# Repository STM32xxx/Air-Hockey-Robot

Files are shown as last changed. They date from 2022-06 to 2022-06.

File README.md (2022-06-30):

# Air-Hockey-Robot
使用OpenCV3 + Arduino mega2560，可与人对战的桌上冰球机器人

展示视频：https://www.bilibili.com/video/BV1ax411d7me?share_source=copy_web

-------------------------------------------------------------------------------------------------------------------------

参考项目：https://github.com/JJulio/AHRobot.git

原项目是国外一个大神做的，相关教程也很详细，链接里文档、视频、源码都有，他的球桌甚至都是自己做的，我也试着用三合板做了个球桌，做的有些大了，而且xy平台用的是H-bot结构，这种结构xy轴是联动的，x轴越长，在快速运动时会产生一个使轴旋转的力，导致高速运动时会卡住。

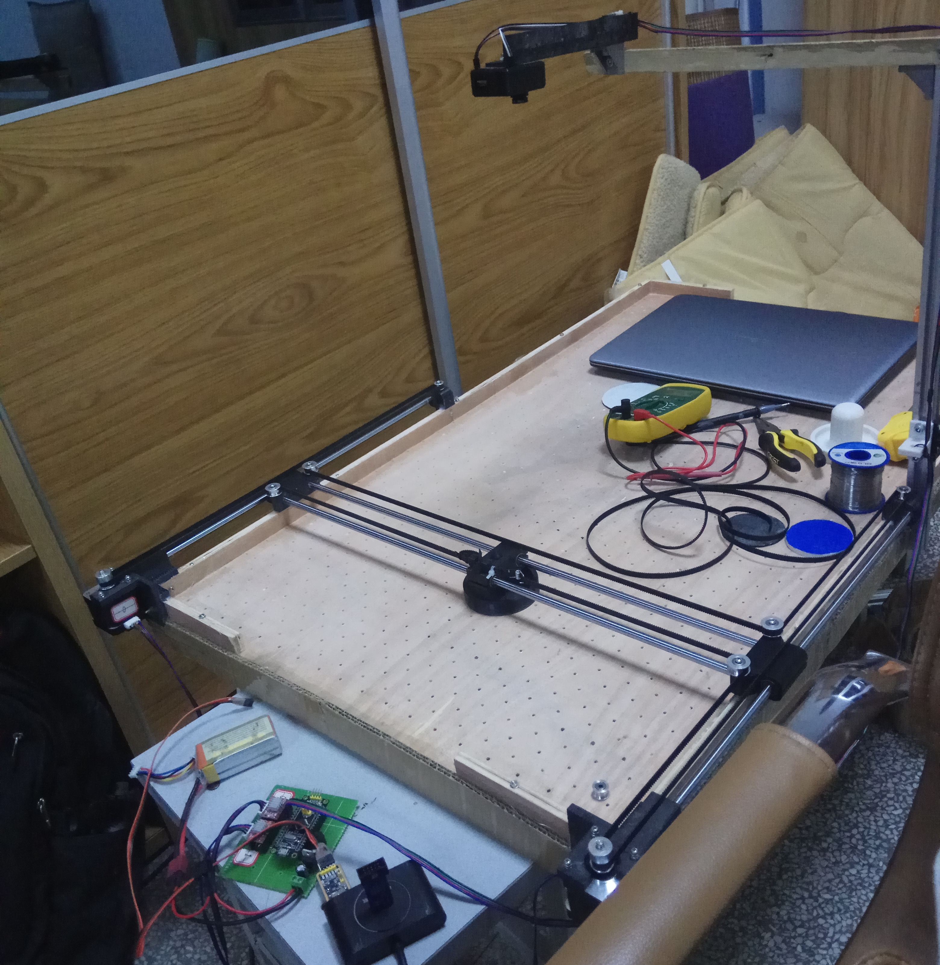
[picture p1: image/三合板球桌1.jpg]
<div align=left>

接下来干脆直接tb买个球桌，长这个样子，81*42cm，比较小，接下来就是将所有机械部分组装上去。

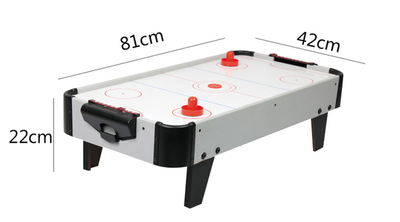
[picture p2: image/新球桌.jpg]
<div align=left>

一些连接件也要自己设计了，用SolidWorks2016设计出以下三维图，黑色的为3D打印件。xy轴是分开控制的，x轴单独由一个电机控制，y轴左右两边各一个电机，这两个电机运动完全同步。

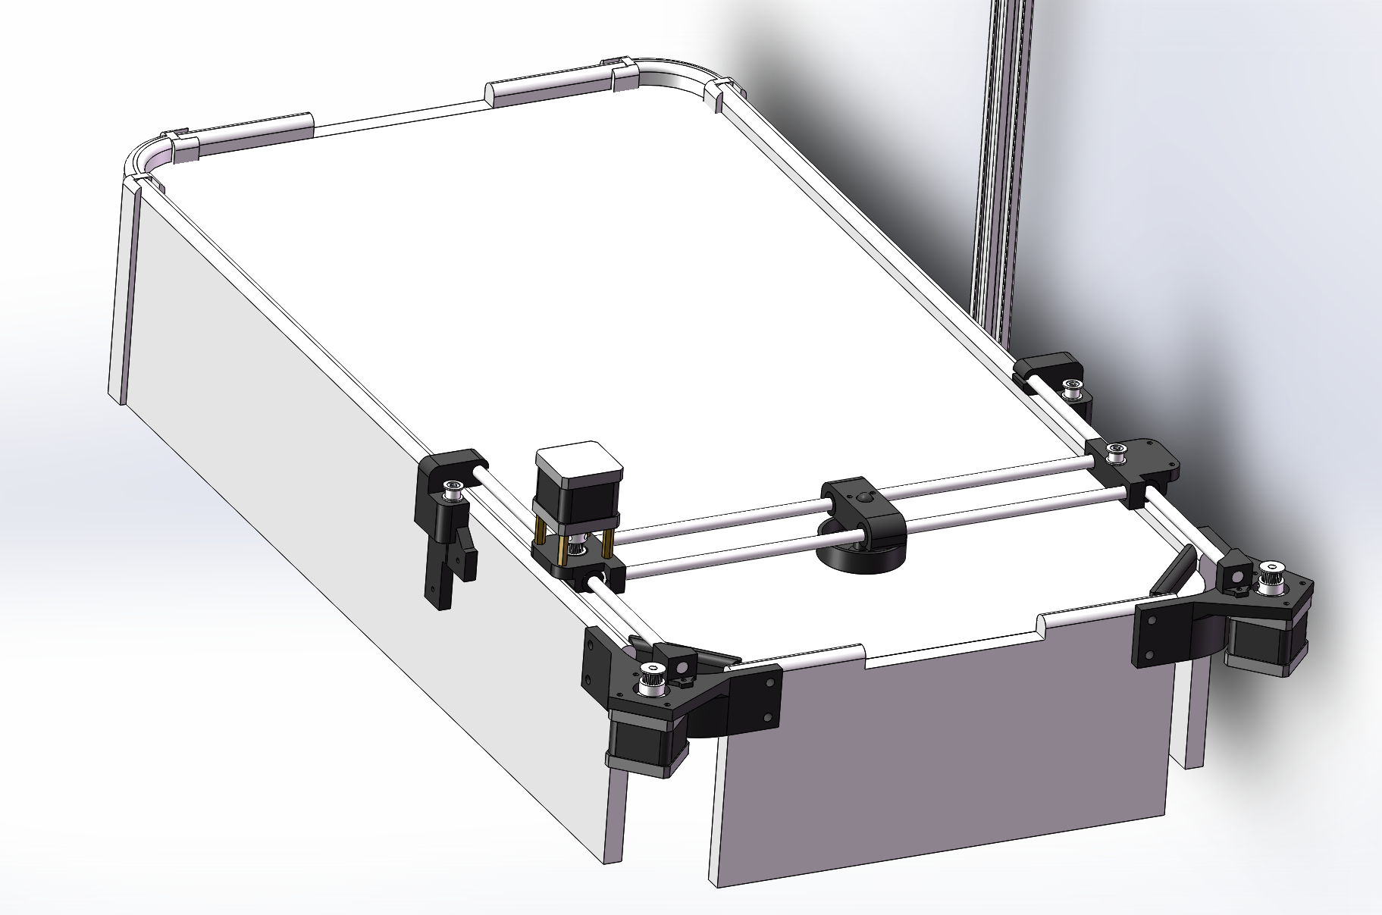
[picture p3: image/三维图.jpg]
<div align=left>

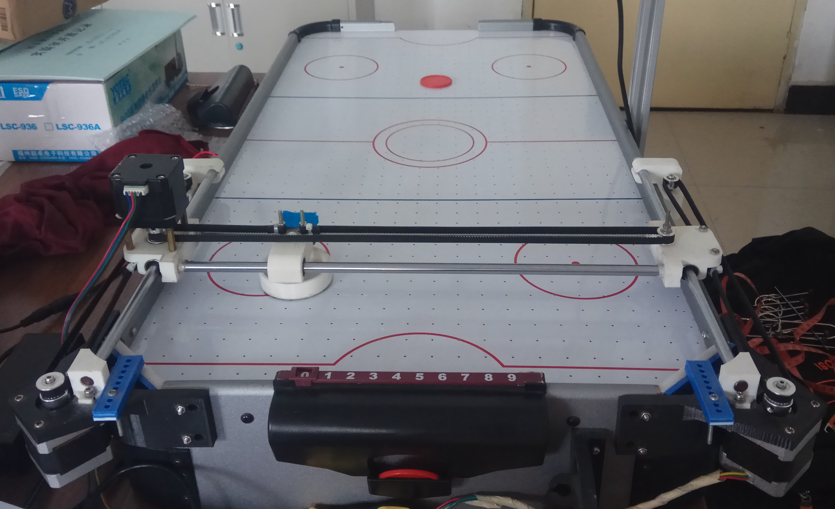
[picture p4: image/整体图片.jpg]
<div align=left>

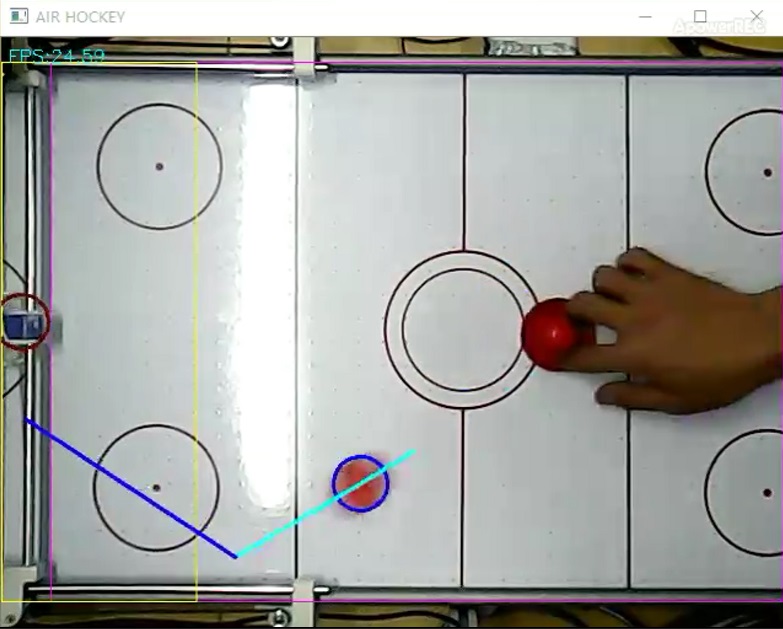
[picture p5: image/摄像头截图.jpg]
<div align=left>

下位机控制采用的arduino mega2560+ramps1.4扩展板，和diy 3d打印机常用的主控一样。

下位机Arduino代码使用的VS2013编译，Arduino官方IDE实在是太难用。Visual Studio安装一个Arduino插件后也可以编译上传Arduino代码。下位机功能类似于GRBL固件，控制击球器点对点移动。与GRBL不同的是，使用GRBL固件时，向下位机发送A点坐标，电机向A点运动，运动期间再发送B点坐标，电机要到达A点之后才会向B点运动。但冰球机器人运动轨迹是上位机来预测的，终点在不断变化，如果还按照GRBL固件来的话会走很多多余路线，也就不能及时抵挡冰球。因此冰球机器人是接收到新的坐标B后便放弃A坐标，立刻向B坐标运动。

上位机图像处理的策略是：通过HSV颜色阈值在画面中寻找冰球和机器人击球器坐标，通过帧差判断出冰球的运动速度和方向，当冰球朝着机器人运动时根据冰球的轨迹预测撞击点坐标（其中包括有反弹和无反弹的情况），将预测的终点坐标发送给下位机，下位机运动到终点视具体情况进行防御或主动进攻。

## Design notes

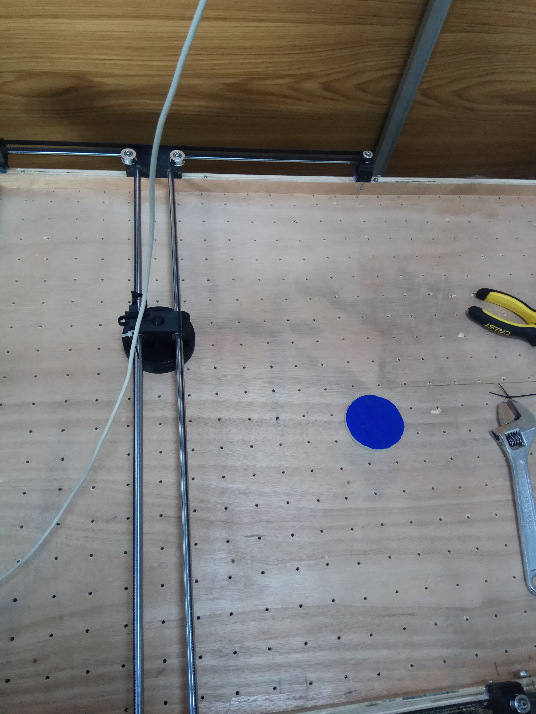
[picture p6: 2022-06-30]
image/三合板球桌2.jpg

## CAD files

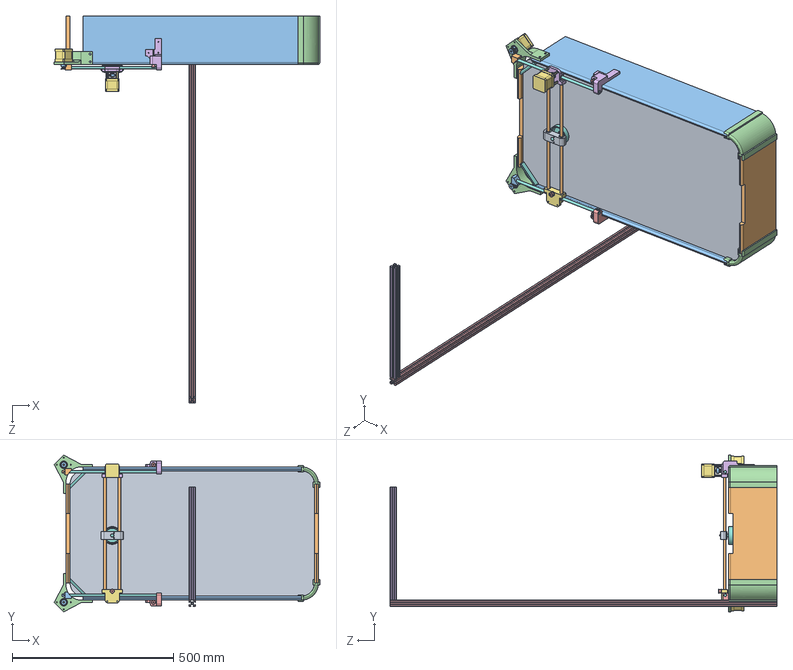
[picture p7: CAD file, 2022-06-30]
冰球机器人三维图v3.0/装配体/装配体.SLDASM
823.4 x 485.9 x 1200.0 mm
桌面
前后侧边 x 2
左右侧边 x 2
倒角 x 2
2020型材
2020型材-2
42步进 x 3
300mm光轴 x 2
LM8UU直线轴承-45mm x 2
450mm光轴 x 2
GT2同步轮内孔5 x 3
LM8UU直线轴承-24mm x 2
惰轮（小） x 3
Y轴滑块-左
Y轴滑块-右
打击器
X轴滑块
Y轴下端
Y轴下端-右
步进电机固定架 x 2
Y轴顶端固定件-右
Y轴顶端固定件-左
铜柱 x 4
机器人侧角件 x 2

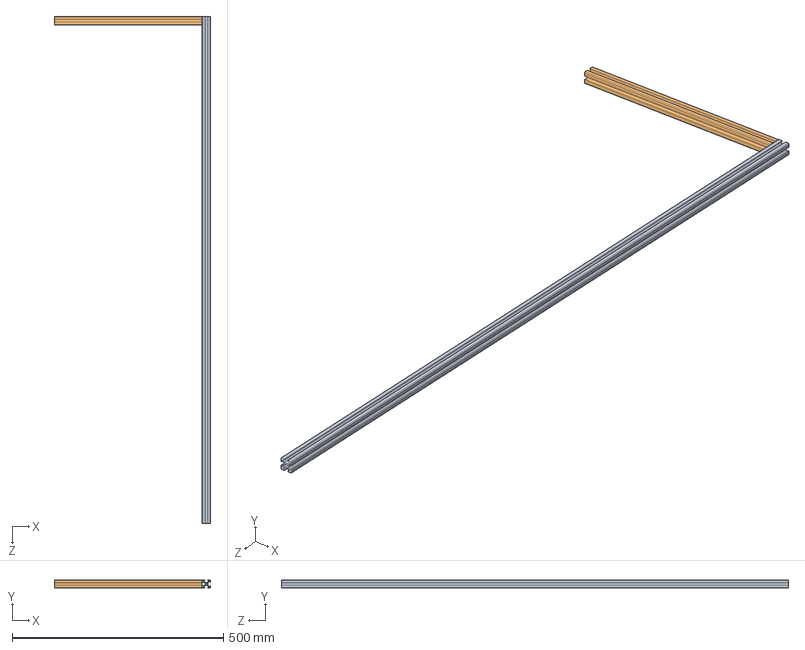
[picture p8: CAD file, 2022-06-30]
冰球机器人三维图v3.0/摄像头支架/摄像头支架装配体.SLDASM
370.0 x 20.0 x 1200.0 mm
2020型材
2020型材-2

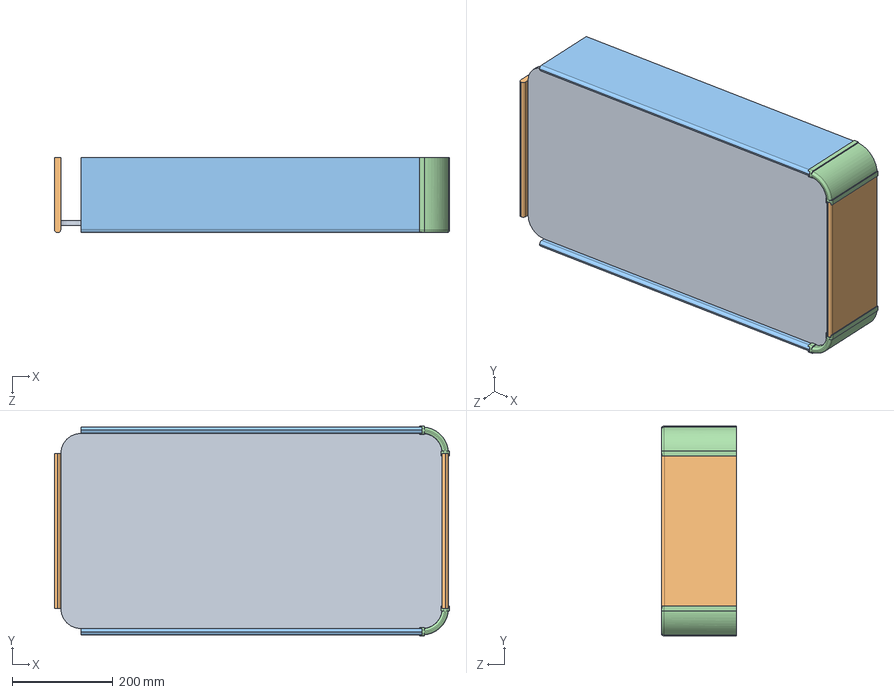
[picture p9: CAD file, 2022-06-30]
冰球机器人三维图v3.0/球桌/球桌装配体.SLDASM
785.0 x 417.0 x 150.0 mm
桌面
前后侧边 x 2
左右侧边 x 2
倒角 x 2

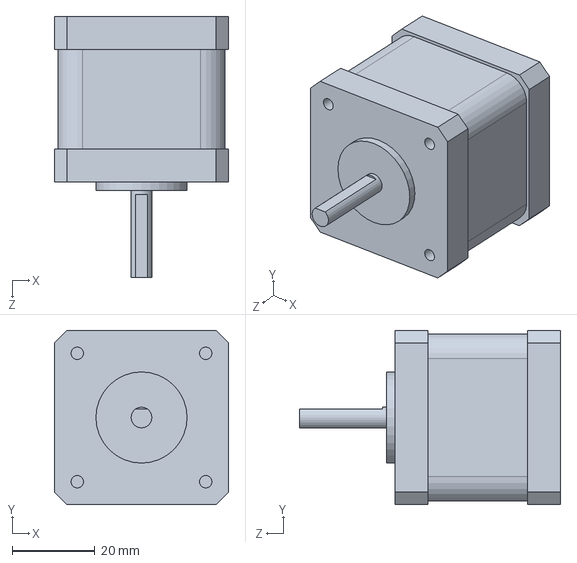
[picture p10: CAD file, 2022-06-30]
冰球机器人三维图v3.0/42步进.SLDPRT
42.0 x 42.0 x 63.0 mm

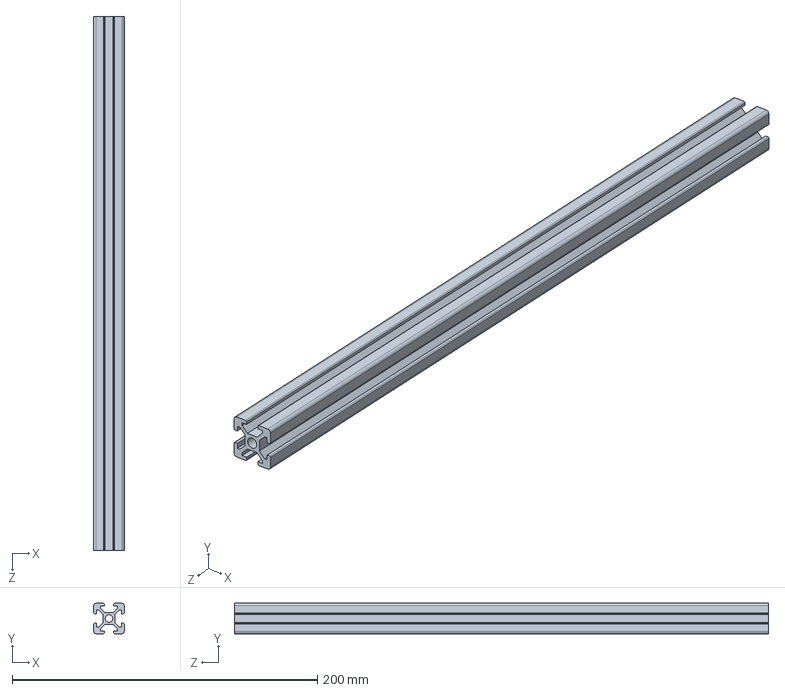
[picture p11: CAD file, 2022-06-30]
冰球机器人三维图v3.0/摄像头支架/2020型材-2.SLDPRT
20.0 x 20.0 x 350.0 mm

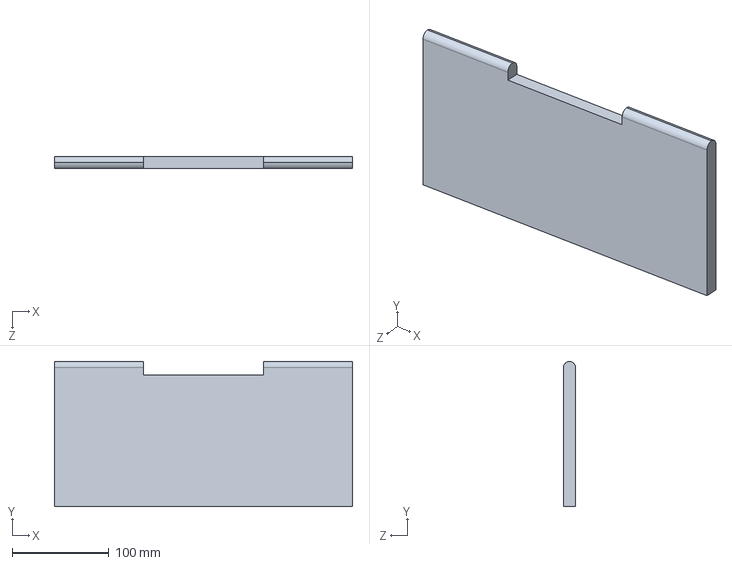
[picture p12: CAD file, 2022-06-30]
冰球机器人三维图v3.0/球桌/前后侧边.SLDPRT
308.0 x 150.0 x 12.5 mm

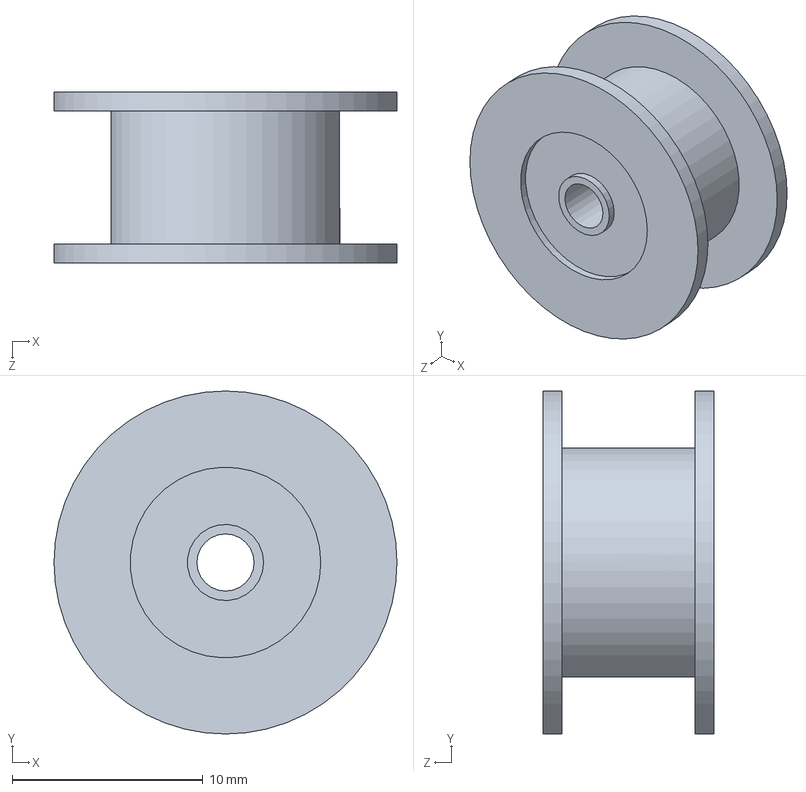
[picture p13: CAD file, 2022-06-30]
冰球机器人三维图v3.0/惰轮（大）.SLDPRT
18.0 x 18.0 x 9.00 mm

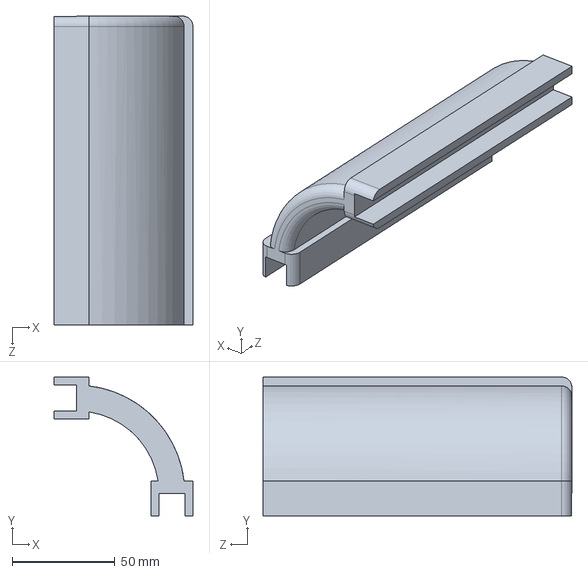
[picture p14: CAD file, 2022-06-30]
冰球机器人三维图v3.0/球桌/倒角.SLDPRT
67.5 x 67.5 x 150.0 mm

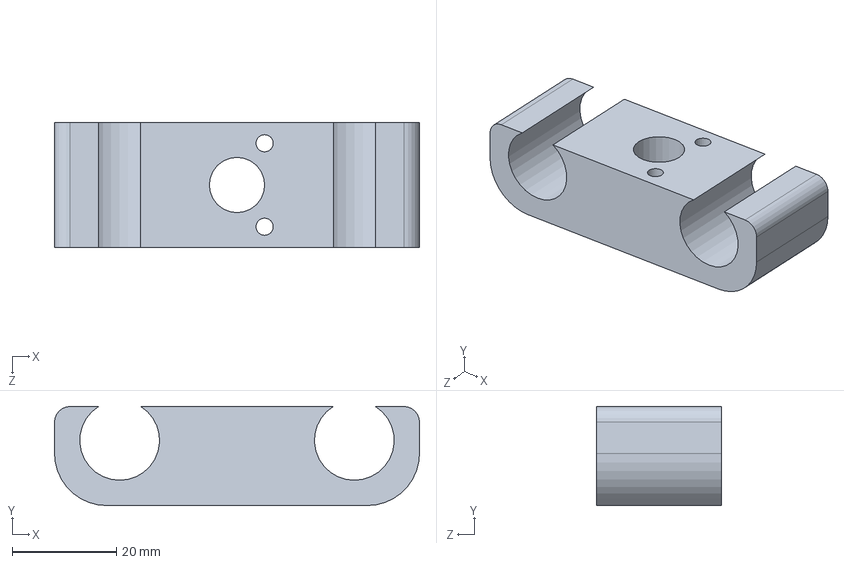
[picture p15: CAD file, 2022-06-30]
冰球机器人三维图v3.0/X轴滑块.SLDPRT
70.0 x 19.0 x 24.0 mm

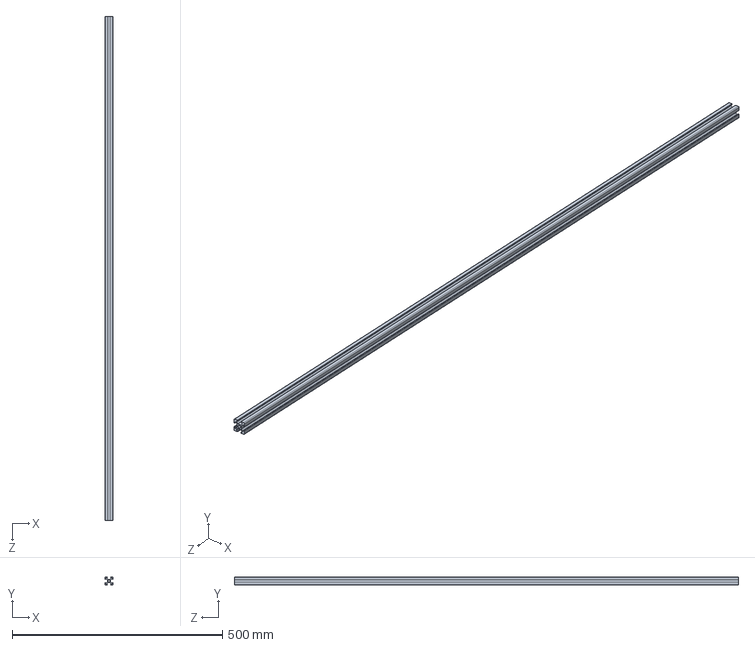
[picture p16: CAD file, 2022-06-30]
冰球机器人三维图v3.0/摄像头支架/2020型材.SLDPRT
20.0 x 20.0 x 1200.0 mm

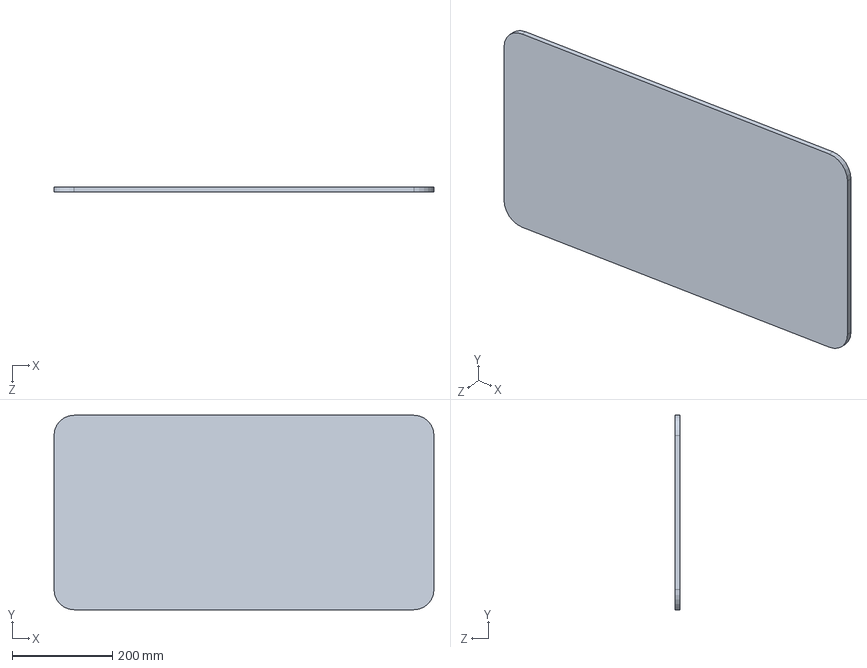
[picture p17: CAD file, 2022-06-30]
冰球机器人三维图v3.0/球桌/桌面.SLDPRT
758.0 x 388.0 x 10.0 mm

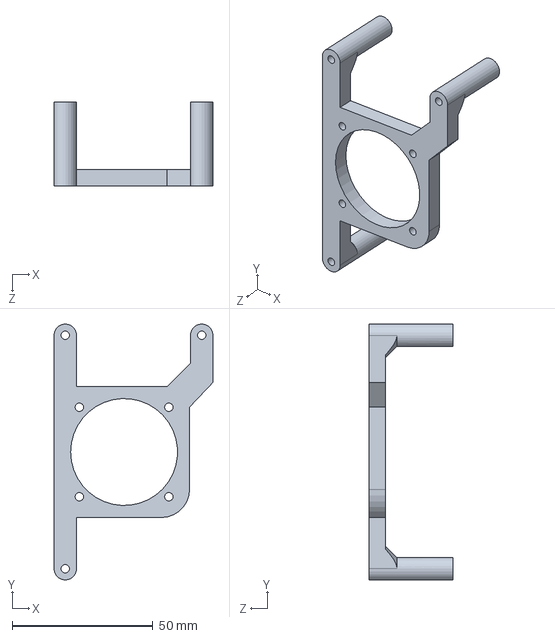
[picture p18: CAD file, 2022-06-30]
冰球机器人三维图v3.0/风扇支架.SLDPRT
56.5 x 91.0 x 30.0 mm

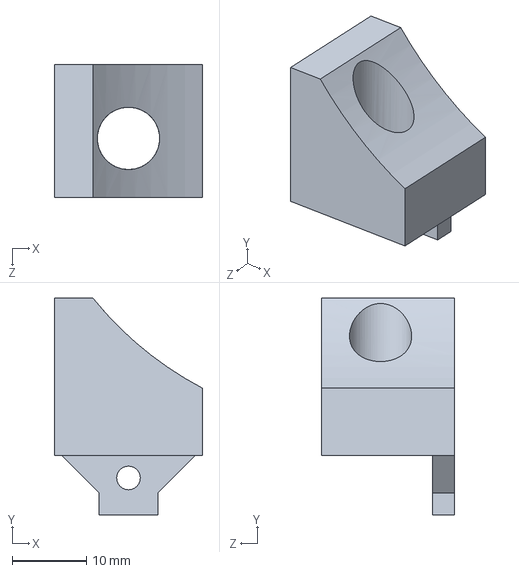
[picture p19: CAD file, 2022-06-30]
冰球机器人三维图v3.0/Y轴下端.SLDPRT
20.0 x 29.3 x 18.0 mm

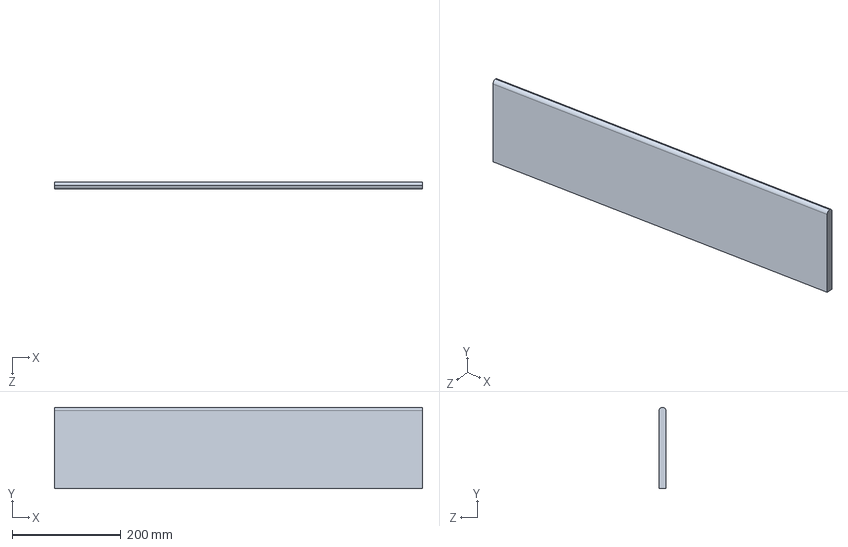
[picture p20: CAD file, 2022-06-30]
冰球机器人三维图v3.0/球桌/左右侧边.SLDPRT
678.0 x 150.0 x 12.5 mm

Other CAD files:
冰球机器人三维图v3.0/Y轴顶端固定件-左.SLDPRT
冰球机器人三维图v3.0/机器人侧角件.SLDPRT
冰球机器人三维图v3.0/GT2同步轮内孔5.SLDPRT
冰球机器人三维图v3.0/Y轴滑块-右.SLDPRT
冰球机器人三维图v3.0/300mm光轴.SLDPRT
冰球机器人三维图v3.0/450mm光轴.SLDPRT
冰球机器人三维图v3.0/600mm.SLDPRT
冰球机器人三维图v3.0/LM8UU直线轴承-24mm.SLDPRT
冰球机器人三维图v3.0/LM8UU直线轴承-45mm.SLDPRT
冰球机器人三维图v3.0/STL/X轴滑块.STL
冰球机器人三维图v3.0/STL/Y轴下端-右.STL
冰球机器人三维图v3.0/STL/Y轴下端.STL
冰球机器人三维图v3.0/STL/Y轴滑块-右.STL
冰球机器人三维图v3.0/STL/Y轴滑块-左.STL
冰球机器人三维图v3.0/STL/Y轴顶端固定件-右.STL
冰球机器人三维图v3.0/STL/Y轴顶端固定件-左.STL
冰球机器人三维图v3.0/STL/打击器.STL
冰球机器人三维图v3.0/STL/机器人侧角件.STL
冰球机器人三维图v3.0/STL/步进电机固定架.STL
冰球机器人三维图v3.0/Y轴下端-右.SLDPRT
冰球机器人三维图v3.0/Y轴滑块-左.SLDPRT
冰球机器人三维图v3.0/Y轴顶端固定件-右.SLDPRT
冰球机器人三维图v3.0/惰轮（小）.SLDPRT
冰球机器人三维图v3.0/打击器.SLDPRT
冰球机器人三维图v3.0/桌上冰球.SLDPRT
冰球机器人三维图v3.0/步进电机固定架.SLDPRT
冰球机器人三维图v3.0/铜柱.SLDPRT

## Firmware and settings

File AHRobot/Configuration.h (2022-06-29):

// AHR AIR HOCKEY ROBOT PROJECT

// USER CONFIGURATIONS HERE
// ROBOT DIMENSIONS, MAX SPEED, MAX ACCELERATION, CALIBRATION

// THIS VALUES DEPENDS ON THE VOLTAGE, MOTORS, PULLEYS AND ROBOT CONSTRUCTION
// RECOMMENDED VALUES FOR 12V POWER SUPPLY
#define MIN_ACCEL_X 60
#define MAX_ACCEL_X 320   //360 //300//320      // Maximun motor acceleration in (steps/seg2)/1000
#define MIN_ACCEL_Y 60
#define MAX_ACCEL_Y 180    //140//220 
#define MAX_SPEED_X 32000     //max 25000 for 12V   // Maximun speed in steps/seg
#define MAX_SPEED_Y 28000

// This is for the Accel ramp implementation (to smooth the intial acceleration), simplified S-profile
#define ACCEL_RAMP_MIN 2500  // The S profile is generated up to this speed
#define ACCEL_RAMP_MAX 10000

// UNCOMMENT THIS LINES TO INVERT MOTORS
#define INVERT_X_AXIS 1
//#define INVERT_Y_AXIS 1  //Y-LEFT
//#define INVERT_Z_AXIS 1  //Y_RIGHT

// Geometric calibration.
// This depends on the pulley teeth. For 42 teeth GT2 => 19, for 40 teeth GT2 => 20, for 16 teeth T5 => 20
#define X_AXIS_STEPS_PER_UNIT 40    // With 42 teeth GT2 pulley and 1/8 microstepping on drivers
#define Y_AXIS_STEPS_PER_UNIT 40    // 200*8 = 1600 steps/rev = 1600/42teeth*2mm = 19.047, using 19 is an error of 1mm every 40cm not too much! and we use int operations...

// Absolute Min and Max robot positions in mm (measured from center of robot pusher)
#define ROBOT_MIN_X 0
#define ROBOT_MIN_Y 0
#define ROBOT_MAX_X 322
#define ROBOT_MAX_Y 400

// This is the center of the table. All units in milimeters
#define ROBOT_CENTER_X 161   // Center of robot. The table is 600x1000mm, so center is 300,500
#define ROBOT_CENTER_Y 0/////////////////////////////////////

// Robot defense and attack lines
#define ROBOT_DEFENSE_POSITION 20 //（单位：mm）
#define ROBOT_DEFENSE_ATTACK_POSITION 110 //最大180，（单位：mm）

//修正电动机的缺失步骤
//如果你不想做修正的话，将宏定义改为0
#define CORRECT_MISSING_STEPS_X 1
#define CORRECT_MISSING_STEPS_Y 0

#define MISSING_STEPS_MAX_ERROR_X 8
#define MISSING_STEPS_MAX_ERROR_Y 10
#define ROBOT_POSITION_CAMERA_CORRECTION_Y -20 // Correction of the position of the camera because the camera point of view and mark position

// AIR HOCKEY TABLE FANS SPEED
// USE 255 for FULL SPEED (if you use 15V power supply 180 is ok)
#define FAN1_SPEED 255  //180
#define FAN2_SPEED 255  //180

// Utils (don´t modify)
#define CLR(x,y) (x&=(~(1<<y)))
#define SET(x,y) (x|=(1<<y))

#define ZERO_SPEED 65535

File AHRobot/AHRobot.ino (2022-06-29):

// AHR: AIR HOCKEY ROBOT PROJECT
// Author: Jose Julio (@jjdrones)
// Hardware: Arduino MEGA + Ramps 1.4
// Date: 18/11/2013
// Last updated: 24/03/2014
// Version: 1.05
// Project page : 
//    Spanish: http://cienciaycacharreo.blogspot.com.es/2014/02/nuevo-proyecto-air-hockey-robot-3d.html 
//    English: http://cienciaycacharreo.blogspot.com.es/2014/02/new-project-air-hockey-robot-3d-printer.html
// GIT repository: https://github.com/JJulio/AHRobot
// License: Open Software GPL License

// ROBOT and USER configuration parameters
#include "Configuration.h"
#include "Definitions.h"   // Variable definitions

void setup() 
{ 
  // STEPPER MOTOR PINS (SAME AS RAMPS 1.4)
  // X MOTOR
  //     X-STEP: A0    (PF0)
  //     X-DIR:  A1    (PF1)
  //     X-ENABLE: D38 (PD7)
  // Y MOTOR (Y-LEFT)
  //     Y-STEP: A6    (PF6)
  //     Y-DIR:  A7    (PF7)
  //     Y-ENABLE: A2  (PF2)
  // Z MOTOR (Y-RIGHT)
  //     Z-STEP: D46   (PL3)
  //     Z-DIR:  D48   (PL1)
  //     Z-ENABLE: A8  (PK0)

  // STEPPER PINS 
  // X_AXIS
  pinMode(38,OUTPUT);  // ENABLE MOTOR
  pinMode(A0,OUTPUT);  // STEP MOTOR
  pinMode(A1,OUTPUT);  // DIR MOTOR
  // Y_AXIS (Y-LEFT)
  pinMode(A2,OUTPUT);  // ENABLE MOTOR
  pinMode(A6,OUTPUT);  // STEP MOTOR
  pinMode(A7,OUTPUT);  // DIR MOTOR
  // Z_AXIS (Y-RIGHT)
  pinMode(A8,OUTPUT);  // ENABLE MOTOR
  pinMode(46,OUTPUT);  // STEP MOTOR
  pinMode(48,OUTPUT);  // DIR MOTOR 

  pinMode(A3,OUTPUT);  // DEBUG PIN FOR OSCILLOSCOPE TIME MEASURES

  pinMode(19,INPUT);  // RX1 Serial Port 1
  pinMode(18,OUTPUT); // TX1

  //FANS and LEDS
  pinMode(8,OUTPUT);
  pinMode(9,OUTPUT);
  pinMode(10,OUTPUT);
  pinMode(13,OUTPUT);

  // Disable Motors
  digitalWrite(38,HIGH);
  digitalWrite(A2,HIGH);
  digitalWrite(A8,HIGH);

  Serial.begin(115200);
  Serial.println("AHR Robot version 1.05");
  delay(100);
  Serial.println("Initializing robot...");
  delay(100);

  cameraProcessInit();  // Camera variable initializations

  //LED blink
  for (uint8_t k=0;k<4;k++)
  {
    digitalWrite(13,HIGH);
    delay(300);
    digitalWrite(13,LOW);
    delay(300);
  } 

  // We use TIMER 1 for stepper motor X AXIS and Timer 3 for Y AXIS
  // STEPPER MOTORS INITIALIZATION
  // TIMER1 CTC MODE
  TCCR1B &= ~(1<<WGM13);
  TCCR1B |=  (1<<WGM12);
  TCCR1A &= ~(1<<WGM11); 
  TCCR1A &= ~(1<<WGM10);

  // output mode = 00 (disconnected)
  TCCR1A &= ~(3<<COM1A0); 
  TCCR1A &= ~(3<<COM1B0); 

  // Set the timer pre-scaler
  // Generally we use a divider of 8, resulting in a 2MHz timer on 16MHz CPU
  TCCR1B = (TCCR1B & ~(0x07<<CS10)) | (2<<CS10);

  OCR1A = ZERO_SPEED;   // Motor stopped
  dir_x = 0;
  TCNT1 = 0;

  // We use TIMER 3 for stepper motor Y AXIS 
  // STEPPER MOTORS INITIALIZATION
  // TIMER3 CTC MODE
  TCCR3B &= ~(1<<WGM13);
  TCCR3B |=  (1<<WGM12);
  TCCR3A &= ~(1<<WGM11); 
  TCCR3A &= ~(1<<WGM10);

  // output mode = 00 (disconnected)
  TCCR3A &= ~(3<<COM1A0); 
  TCCR3A &= ~(3<<COM1B0); 

  // Set the timer pre-scaler
  // Generally we use a divider of 8, resulting in a 2MHz timer on 16MHz CPU
  TCCR3B = (TCCR3B & ~(0x07<<CS10)) | (2<<CS10);

  OCR3A = ZERO_SPEED;   // Motor stopped
  dir_y = 0;
  TCNT3 = 0;

  delay(100);

  Serial.println("Initializing Stepper motors...");
  delay(100);
  TIMSK1 |= (1<<OCIE1A);  // Enable Timer1 interrupt
  TIMSK3 |= (1<<OCIE1A);  // Enable Timer1 interrupt

  // Enable steppers
  digitalWrite(38,LOW);   // X-axis
  digitalWrite(A2,LOW);   // Y-axis left
  digitalWrite(A8,LOW);   // Z-axis (Y-axis right)

  // Output parameters
  Serial.print("Max_acceleration_x: ");
  Serial.println(max_acceleration_x);
  Serial.print("Max_acceleration_y: ");
  Serial.println(max_acceleration_y);
  Serial.print("Max speed X: ");
  Serial.println(MAX_SPEED_X);
  Serial.print("Max speed Y: ");
  Serial.println(MAX_SPEED_Y);
  Serial.println("Moving to initial position...");
  Serial.println("Ready!!");
  delay(100);

  // Enable Air Hockey FANS
  //digitalWrite(9,HIGH);
  //digitalWrite(10,HIGH);
  analogWrite(9, FAN1_SPEED);
  analogWrite(10, FAN2_SPEED);

  position_x = ROBOT_CENTER_X*X_AXIS_STEPS_PER_UNIT;
  position_y = ROBOT_DEFENSE_POSITION*Y_AXIS_STEPS_PER_UNIT;

  timer_old = micros();
  timer_packet_old = timer_old;
  micros_old = timer_old;
}

void loop()
{
	//int dt;
	debug_counter++;
	timer_value = micros();//获取开机时间
	if ((timer_value-timer_old)>=1000)  // 1Khz循环
	{
		//dt = (timer_value-timer_old)/1000;
		timer_old = timer_value;

		loop_counter++;//循环次数+1

		packetRead();//读取串口
		if (newPacket)//接收到新消息
		{
		//	dt = (timer_value-timer_packet_old)/1000.0;
		//	dt = 16;  //60 Hz = 16.66ms
			newPacket=0;

			robot_status = (uint8_t)puckSize;
			predict_x = (puckPixX - 51) / 1.15528;
			predict_y = (puckPixY - 13) / 1.15385 + 20;

			missingStepsDetection(robotPixX, robotPixY);//检测步进丢失位移并校正
		}

		robotStrategy();//策略：机器人行为

		positionControl();//位置控制输出
	}
}

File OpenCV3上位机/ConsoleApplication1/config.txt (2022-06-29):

# AHR_EVO configuration file 

CAMERA 1         # 0=FIRST CAMERA, 1=SECOND CAMERA, -1=OPEN "input.mpeg" file video

SERIALPORT 5

PUCKMINH 0      # PUCK HSV DETECTION PARAMETERS

PUCKMAXH 179

PUCKMINS 82

PUCKMAXS 255

PUCKMINV 101

PUCKMAXV 255

ROBOTMINH 100      # ROBOT HSV DETECTION PARAMETERS

ROBOTMAXH 179

ROBOTMINS 70

ROBOTMAXS 255

ROBOTMINV 0

ROBOTMAXV 255


VIDEOOUTPUT YES  # YES or NO

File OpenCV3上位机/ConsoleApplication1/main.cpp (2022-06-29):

#include "iostream"
#include "opencv2/imgproc/imgproc.hpp"
#include "opencv2/highgui/highgui.hpp" 
#include "opencv2/core/core.hpp"

#include "serialport.h"

using namespace cv;
using namespace std;

#define RESOLUTION_X 640 //设定摄像头参数，单位为像素
#define RESOLUTION_Y 480 //设定摄像头参数，单位为像素
#define FPS 60 //摄像头帧率

#define CONSTRAIN(amt,low,high) ((amt)<(low)?(low):((amt)>(high)?(high):(amt))) //限制参数范围
#define PUCK_LEFT_CONFINE 51 //冰球在摄像头视野中最小x坐标（单位：像素）
#define PUCK_RIGHT_CONFINE 423 //冰球在摄像头视野中最小y坐标（单位：像素）
#define DEFENSE_POSITION 20 //防御线y坐标（单位：像素）
#define ATTACK_POSITION 120 //进攻线y坐标（单位：像素）

//图像变量
Mat frame, imgHSV;
Mat imgThresh, imgThresh2;

//保存串口向下位机发送的指令
unsigned char coordResult[20] = { "\0" };

//寻找冰球和机器人变量
int RobotCoordX = 0;//机器人实时x坐标
int RobotCoordY = 0;//机器人实时y坐标
int puckCoordX = 0;//冰球实时x坐标
int puckCoordY = 0;//冰球实时y坐标
int puckOldCoordX = 0;//冰球上次x坐标
int puckOldCoordY = 0;//冰球上次x坐标
int puckSpeedX = 0;//冰球在x轴上的实时速度
int puckSpeedY = 0;//冰球在y轴上的实时速度
int puckOldSpeedX = 0;//冰球在x轴上的上次速度
int puckOldSpeedY = 0;//冰球在y轴上的上次速度
int puckSpeedXAverage = 0;//冰球在x轴平均速度
int puckSpeedYAverage = 0;//冰球在y轴平均速度
int predict_x = 0;//预测冰球进入到机器人防御线时的x坐标
int predict_y = 0;//预测冰球进入到机器人防御线时的y坐标
int predict_x_old = 0;//保存上次预测的冰球到达机器人防御线时的x坐标
int predict_x_attack = 0;//预测冰球运动到机器人进攻线时的x坐标
int predict_status = 0;// -1：噪声 0：冰球移动缓慢或者正向人移动 1：冰球直线运动到目标 2：冰球与侧边发生了一次碰撞

//读取配置文件变量
int camera_cap;
int serial_port;
int minH,maxH,minS,maxS,minV,maxV;
int RminH,RmaxH,RminS,RmaxS,RminV,RmaxV;
bool log_output;
bool video_output;

//主动进攻模式变量
long attack_time = 0;
int attack_pos_x = 0;
int attack_pos_y =0;
int attack_predict_x = 0;
int attack_predict_y = 0;
int attack_status = 0;

//关于时间的预测
int predict_time = 0;//预测冰球到达机器人防御线的时间，单位ms
int predict_time_attack = 0;//预测冰球到达机器人进攻线的时间，单位ms

//与计算帧率有关变量
double firstTime = 0;//记录首次时间
double realTime = 0;//记录实时时间
double realTime_old = 0;//记录上次实时时间
int run_counter = 0;//记录程序运行的次数

//显示FPS
double fps;
char str[10];  // 用于存放帧率的字符串
string fpsString("FPS:");

//用于计算机器人策略
unsigned char robot_status = 0;//保存机器人应执行的策略

//感兴趣区域
Rect Hockey(40, 20, 600, 440);//寻找冰球感兴趣区域
//Rect Robot(0, 20, 60, 440);//寻找机器人感兴趣区域
Rect Robot(0, 20, 160, 440);//寻找机器人感兴趣区域

//声明串口对象
CSerialPort mySerialPort;

void serialPortInit(UINT com)
{
	if (!mySerialPort.InitPort(com))//打开串口
	{
		std::cout << "initPort fail !" << std::endl;
	}
	else
	{
		std::cout << "initPort success !" << std::endl;
	}

	if (!mySerialPort.OpenListenThread())//打开监听线程
	{
		std::cout << "OpenListenThread fail !" << std::endl;
	}
	else
	{
		std::cout << "OpenListenThread success !" << std::endl;
	}
}

void cameraProcess(float time)
{
	int vectorX;//冰球在两帧图片上x方向位移差
	int vectorY;//冰球在两帧图片上y方向位移差
	double slope;//轨迹斜率

	int bounce_x;//冰球与边界撞击点x坐标
	int bounce_y;//冰球与边界撞击点y坐标

	vectorX = puckCoordX - puckOldCoordX;//位移差，交换xy坐标后
	vectorY = puckCoordY - puckOldCoordY;//位移差，交换xy坐标后

	puckOldSpeedX = puckSpeedX;//将实时速度赋给上次速度
	puckOldSpeedY = puckSpeedY;//将实时速度赋给上次速度

	//更新速度值
	puckSpeedX = vectorX * 100L / time;//每秒30帧
	puckSpeedY = vectorY * 100L / time;//每秒30帧

	//if ((puckSpeedX < -500) || (puckSpeedX > 500) || (puckSpeedY < -500) || (puckSpeedY > 500))//***********************************************************
	//{
	//	//cout << "********noise********" << endl;
	//	predict_status = -1;
	//	predict_x_old = -1;
	//	return;
	//}

	//if (predict_status == -1)// Noise on last reading?  上次阅读的噪音？
	//{
	//	puckSpeedXAverage = puckSpeedX;
	//	puckSpeedYAverage = puckSpeedY;
	//}
	//else
	//{
	//	// if there are low accelerations (similar speeds on readings) we apply an average filtering with the previous value...
	//	//如果有较低的加速度（类似的读数），我们应用一个与先前值的平均过滤。
	//	if (abs(puckSpeedX - puckOldSpeedX) < 50)//***************************************************************************************************
	//		puckSpeedXAverage = (puckSpeedX + puckOldSpeedX) >> 1;
	//	else
	//		puckSpeedXAverage = puckSpeedX;

	//	if (abs(puckSpeedY - puckOldSpeedY) < 50)//***************************************************************************************************
	//		puckSpeedYAverage = (puckSpeedY + puckOldSpeedY) >> 1;
	//	else
	//		puckSpeedYAverage = puckSpeedY;
	//}

		puckSpeedXAverage = puckSpeedX;
		puckSpeedYAverage = puckSpeedY;

	predict_x_attack = -1;//

	//冰球来了
	if (puckSpeedYAverage < -20)//********************************************************************************************************************
	{
		predict_status = 1;

		if (vectorX == 0) slope = 999999;
		else slope = (float)vectorY / (float)vectorX;

		predict_y = DEFENSE_POSITION;//冰球最终目标点的y坐标
		predict_x = (predict_y - puckCoordY) / slope + puckCoordX;//冰球最终目标点的x坐标

		predict_x_attack = (ATTACK_POSITION - puckCoordY) / slope + puckCoordX;//冰球运动到进攻线时的x坐标

		if ((predict_x < PUCK_LEFT_CONFINE) || (predict_x > PUCK_RIGHT_CONFINE))//冰球与侧边发生碰撞
		{
			predict_status = 2;
			//predict_bounce = 1;
			//predict_bounce_status = 1;

			if (predict_x < PUCK_LEFT_CONFINE)//判断与那个侧边发生碰撞
				bounce_x = PUCK_LEFT_CONFINE;
			else
				bounce_x = PUCK_RIGHT_CONFINE;

			bounce_y = (bounce_x - puckCoordX)*slope + puckCoordY;//计算撞击点y坐标
			predict_time = (bounce_y - puckCoordY) * 100L / puckSpeedY;  // time until bouce

			slope = -slope;
			predict_y = DEFENSE_POSITION;
			predict_x = (predict_y - bounce_y) / slope + bounce_x;

			if ((predict_x < PUCK_LEFT_CONFINE) || (predict_x > PUCK_RIGHT_CONFINE)) // New bounce with side wall?
			{
				//我们什么也不做。有了两次反弹，目标的风险很小。
				predict_x_old = -1;
				predict_status = 0;
			}
			else
			{
				////只有一次反弹……
				////如果球速改变了很多这就意味着冰球已经触到了一边
				//if (abs(puckSpeedY - puckOldSpeedY) > 40)//**************************************************************************************************
				//{
				//	// We dont make a new prediction...  不做一个新的预测。
				//	//predict_x_old = -1;
				//}
				//else
				//{
					 //average of the results (some noise filtering)  平均结果（一些噪声滤波）
					if (predict_x_old != -1)
						predict_x = (predict_x_old + predict_x) >> 1;
					predict_x_old = predict_x;

					//我们引入一个因子（120而不是100）来模拟反弹（速度损失20%）
					predict_time = predict_time + (predict_y - puckCoordY) * 130L / puckSpeedY;  // in ms
				//}
			}
			cv::line(frame, Point(puckCoordY, puckCoordX), Point(bounce_y, bounce_x), Scalar(255, 255, 0), 2);
			cv::line(frame, Point(bounce_y, bounce_x), Point(predict_y, predict_x), Scalar(255, 0, 0), 2);
		}
		else  //冰球没有撞到侧边，直接过来
		{
			//if (predict_bounce_status == 1)
			//{
			//	// We dont predict nothing new...
			//	predict_bounce_status = 0;
			//}
			//else
			//{
				// average of the results (some noise filtering)  结果的平均值（一些噪声滤波）
				if (predict_x_old != -1)
					predict_x = (predict_x_old + predict_x) >> 1;
				predict_x_old = predict_x;

				predict_time = (predict_y - puckCoordY) * 100L / puckSpeedY;  // in ms
				predict_time_attack = (ATTACK_POSITION - puckCoordY) * 100L / puckSpeedY; // in ms
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
